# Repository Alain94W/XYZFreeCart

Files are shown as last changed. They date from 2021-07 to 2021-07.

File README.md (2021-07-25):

## XYZ Davinci FreeCart

If you are like me bored about having to reset the cartridge chip with an external computer, then this git can maybe help you.

<b> DISCLAIMER
  
I will take no responsibilities about what you are doing with this or what will happen with this, if you burn your printer, get injury or everything else, don't blame me, your choice, your responsibilities.
I made it for fun, it is working well on my printer (DaVinCi AIO 1.0), I only share for free my work and by the way I don't want to see this work being resell on ebay or on other eshop web site.
</b>

That said ...

<p align="center" width="100%">
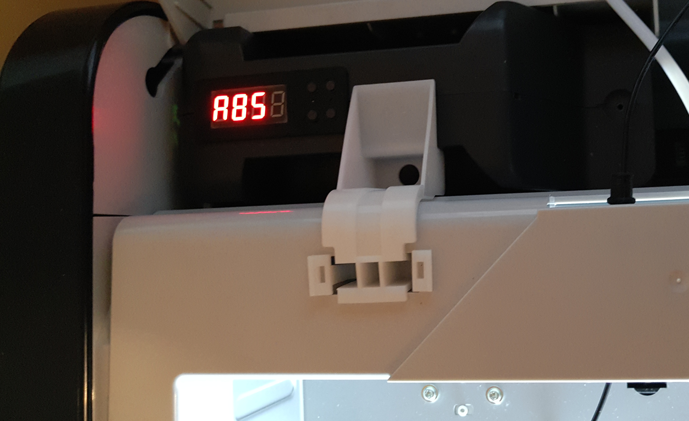
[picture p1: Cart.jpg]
cart
  
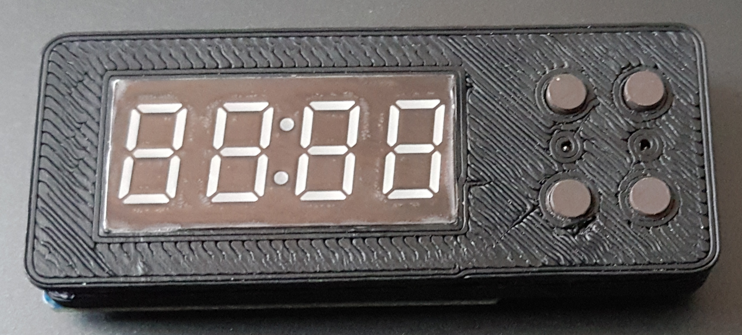
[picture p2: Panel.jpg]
  
</p>

## History of the project
I was using for a long time the arduino reseter made by votivo (by the way, thanks to him for he's work), I was stuck on a PLA filament bought on Amazon (Amazon Basics) The filament always clog the nozzle, I had to play a lot with the extruder temperature and all the time had to reprogram the cartridge chip.
To get ride of this, I used a raspberry pico and a 4*7 Digit LED display (TM1637) and using 4 buttons, I made an EEPROM emulator that I put directly inside the original cartridge.

## The Arm choice 

Because I need a fast microcontroller, cheap and 3.3V level for that task, I've choose the Raspberry Pi Pico.
The raspberry pico is very powerful, but to achieve my project, I had to overclock it to 291MHz and to use both core to run the code.
On Core 0, the UNIO Slave driver is running, waiting for some command coming from the printer (not using pio because of the UNIO protocol specifications). 
On Core 1, the button and display are handled.

The content of the original EEPROM was dump from a PLA's cartridge chip and is written in the flash memory of the pico. When the program start, the FLASH is loaded into the RAM, every time the printer is writing the length update into the cartridge chip, the pico update it's RAM then save it to it's FLASH.

The TM1637 (bought on Amazon) is used to allow the user to changes this settings directly from the cartridge:

<li> Bed Temperature </li>
<li> Extruder Temperature </li>
<li> Filement color </li>
<li> Type of Material </li>
<li> Display and or reset the remaining filament length </li>

When changing bed/extruder temp or color, you can save this settings as a profile for the selected material, there is already a set of profile made in the pico for example :

<li>ABS => Bed : 90*C, Extruder : 210*C, Color : Green </li>
<li>PLA => Bed : 45*C, Extruder : 195*C, Color : Yellow </li>

The available material are :

<li>ABS</li>
<li>PLA</li>
<li>FLEX</li>
<li>PETG</li>
<li>Water Soluble</li>
<li>UVCR</li>
<li>NYLON</li>
<li>ASA</li>

The are 4 buttons used to select the menu, change settings and reset the length:

* SEL : Choose menu (Bed, Head, Colo, Mat, Fil)
* UP/DOWN : to increase and decease the values or change items
* RESET : press less than 3sec => Save settings in the FLASH, Press >3s, reset the spool len and change the serial number.

If you have an unknown filament error on the printer, just press 4sec the Reset button, this will change the serial number.
Every changes made in the menu should be immediately visible in the cart INFO menu of the printer.
Do not reset or change the settings while the printer is printing as it may fail your printing job.

## Printer firmware

I'm using the original factory shipped firmware on my printer, it is an old one, the version <b>1.1.3</b>, I didn't test this on other version or printer model.

## Installation

First, this suppose that you already follow the raspberry pi procedure and you already have the pico-sdk installed.
Then, git clone this repo and go into the root folder.

Edit the CMakeLists.txt on line 10, change the SDK path with your own SDK Path.

Run the following command to compil the pico code :

```
mkdir build
cd build
cmake ..
make
```

This will end up and create a freecart.uf2 file that you can load via the USB to the pico (in boot mode).

<b> NEVER CONNECT THE USB HOST ON THE PICO WHILE IT IS CONNECTED TO THE PRINTER, the printer is 3.3V level and the main board will be destroyed by the 5V injection coming from the USB over the VSYS line of the PICO. </b> If you really want to connect both, read carefully the pico's datasheet, thee are some solution using external schotky diode or mosfet.

## TM1637 Display driver

I used a library made by wahlencraft to drive the TM1637 display, you can find more information here on it's github : https://github.com/wahlencraft/TM1637-pico.git

Thanks for this work, it is included in this repo but I would like to credit wahlencraft for that work.

## Assembly

The step files are in this repo.
I printed them in ABS with a fill density of 50% and a layer height of 0.3 with support material.
You need to cut the cartridge where you want place the control panel, over the EEPROM PCB to make a path for the cables.

<p align="center" width="100%">
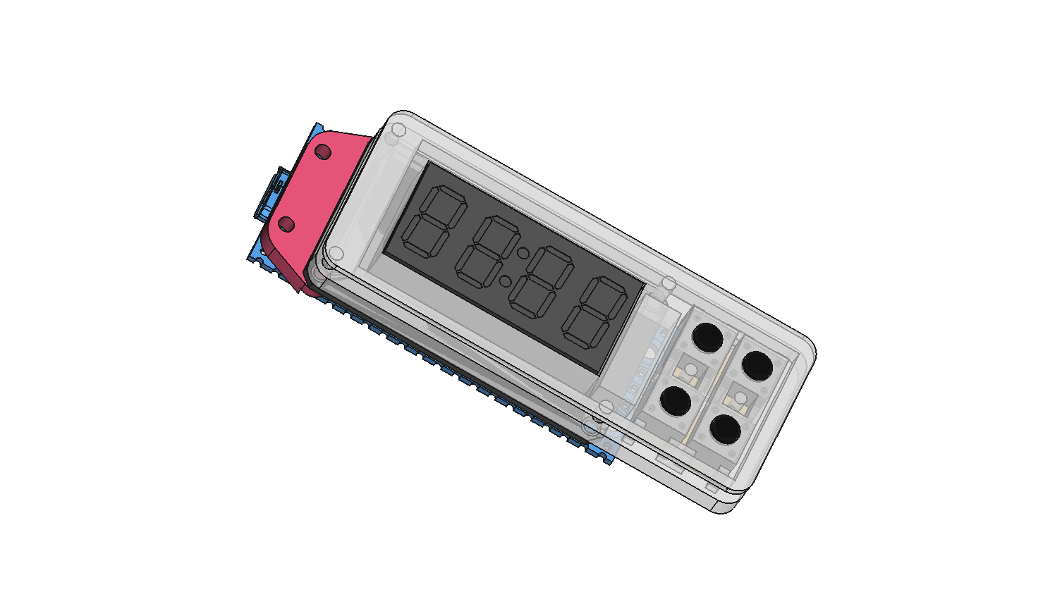
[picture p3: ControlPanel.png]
3dparts
  
</p>

<p align="center" width="100%">
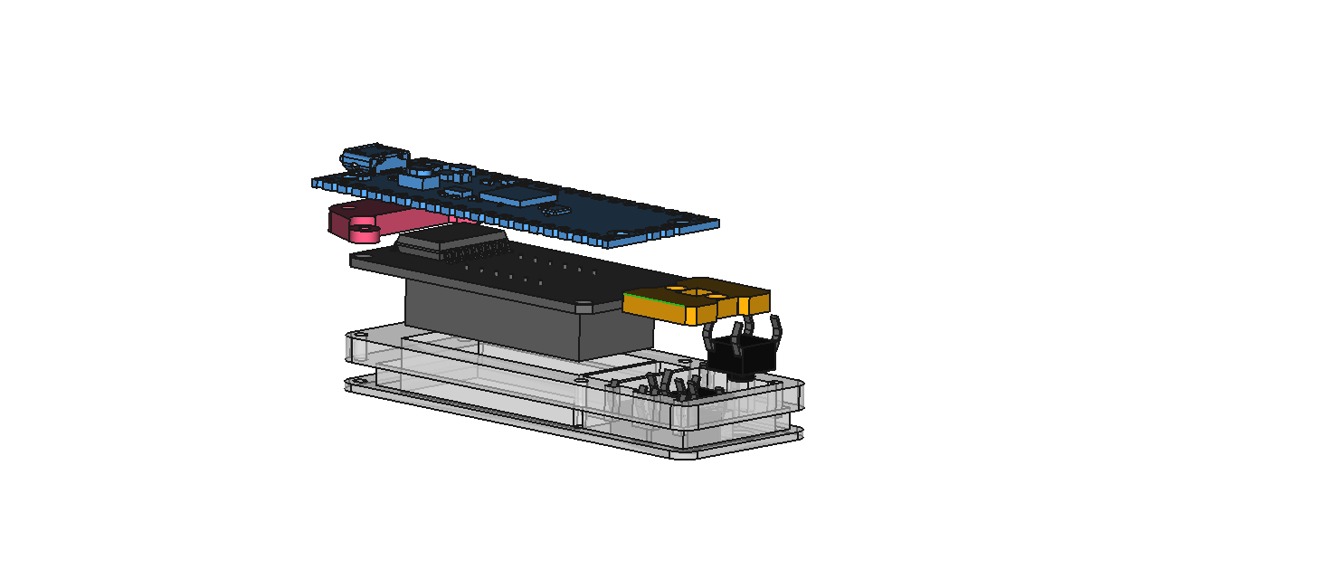
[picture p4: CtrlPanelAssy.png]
Assy
  
</p>

<p align="center" width="100%">
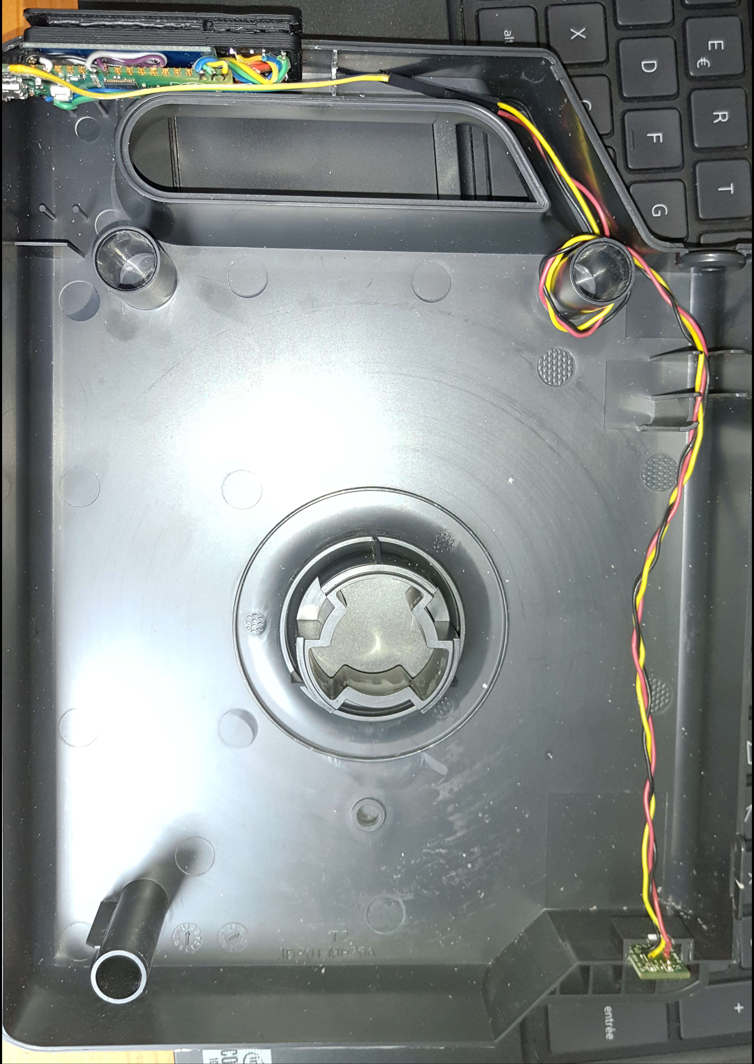
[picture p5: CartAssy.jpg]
Assy
  
</p>

You will need to "sacrifice" an original EEPROM from one of your cartridge, you will have to remove the EEPROM from the PCB and to solder 3 wire directly in place of.

<p align="center" width="100%">
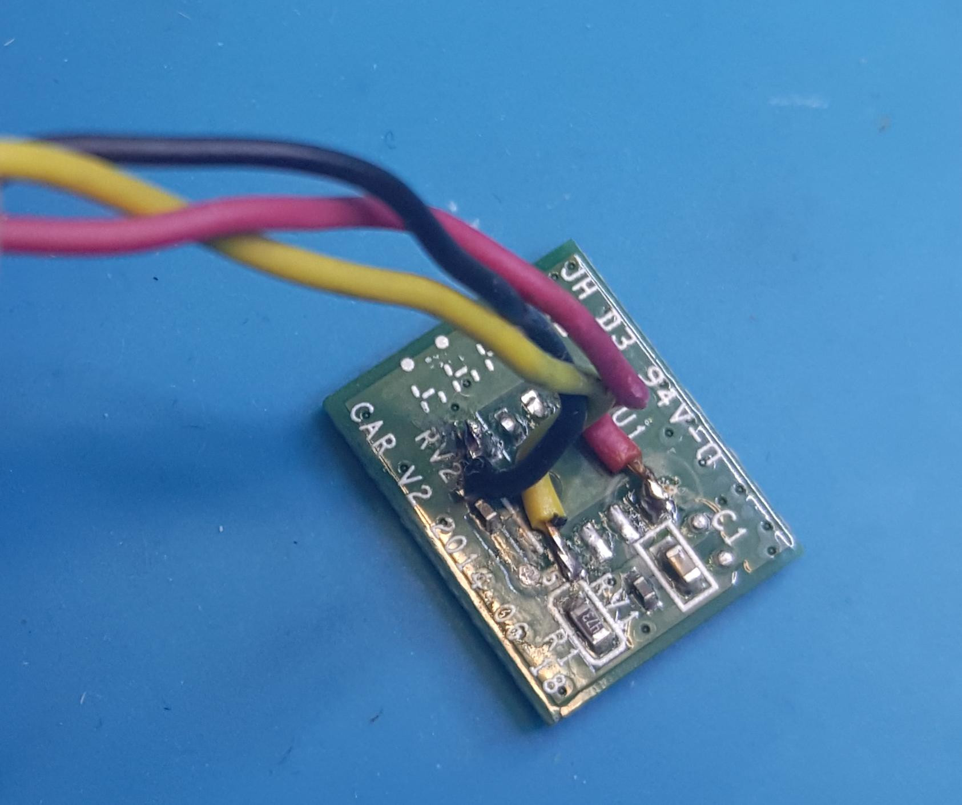
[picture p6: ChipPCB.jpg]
  
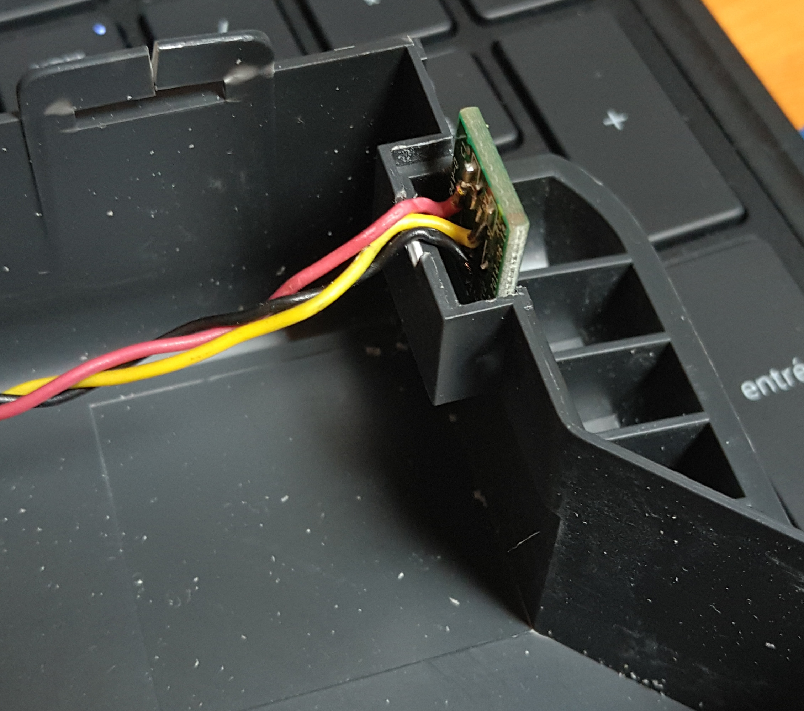
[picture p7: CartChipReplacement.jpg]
  
</p>

You have to wire everything like this:

<p align="center" width="100%">
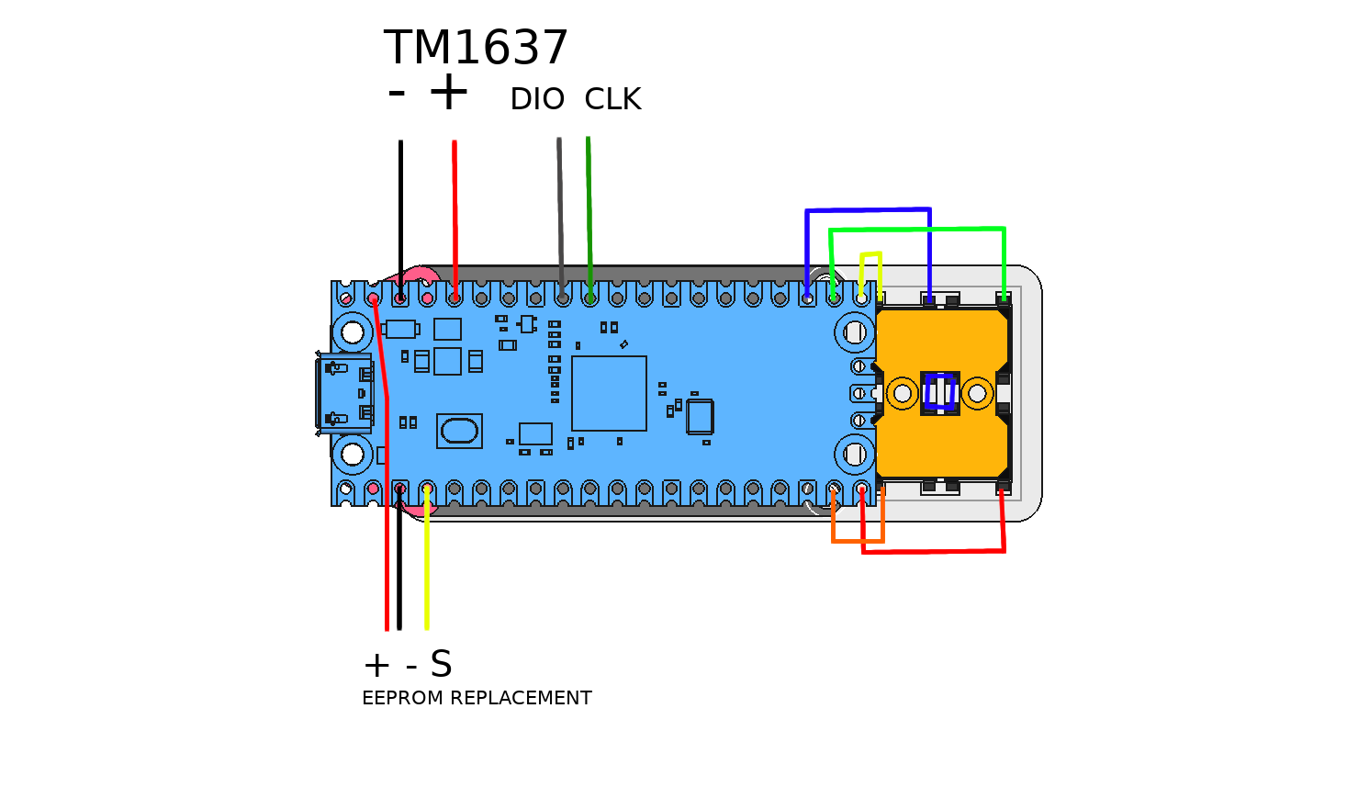
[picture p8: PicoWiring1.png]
picowiring
  
</p>

## Button disposition

<p align="center" width="100%">
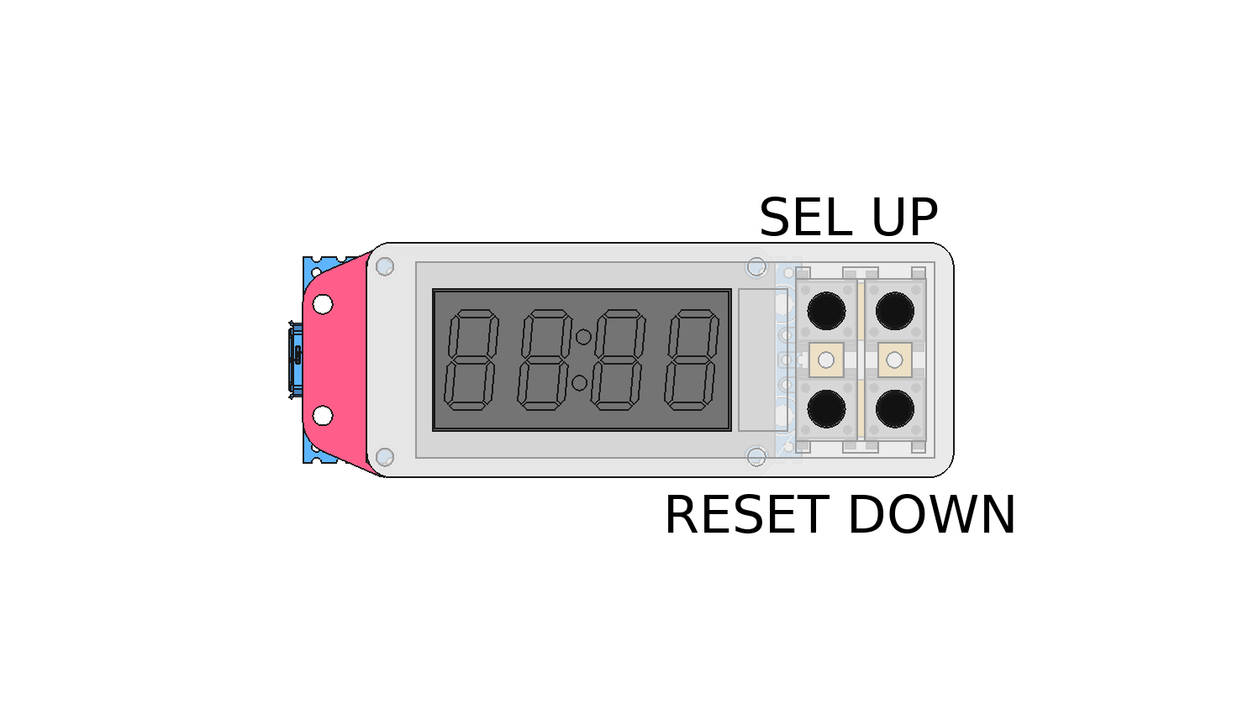
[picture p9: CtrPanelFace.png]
  
</p>

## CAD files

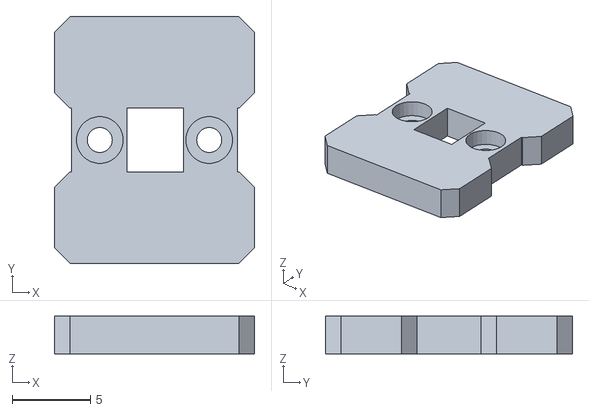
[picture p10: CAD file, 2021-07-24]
3DParts/ControlPanel-BtnLockPlate.stl
12.8 x 15.8 x 2.40

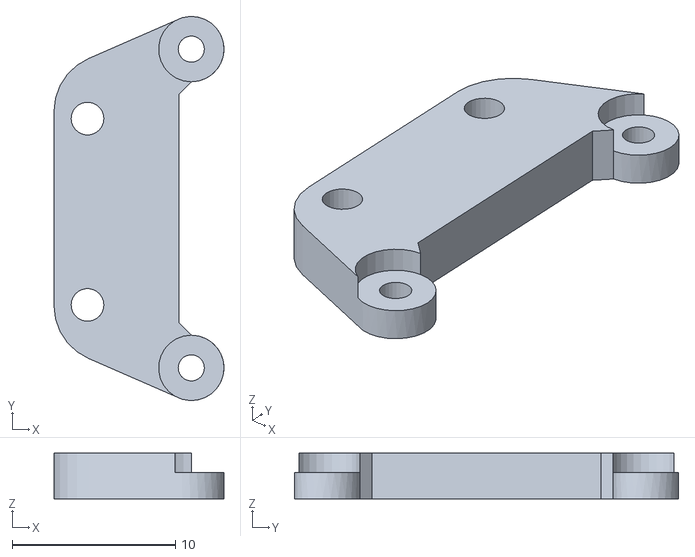
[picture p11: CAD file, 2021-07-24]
3DParts/ControlPanel-PicoFixPlateUSBSide.stl
10.4 x 23.5 x 2.80

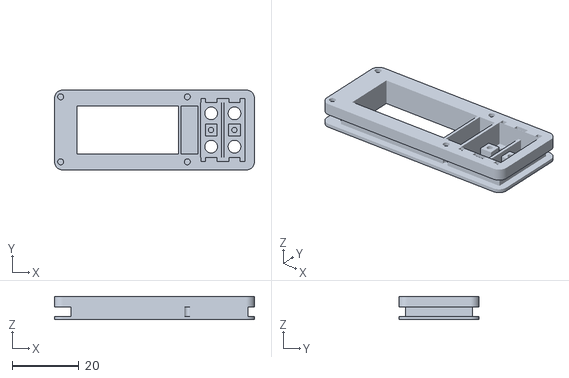
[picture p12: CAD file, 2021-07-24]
3DParts/ControlPanel-BodyPocket006.stl
60.0 x 24.0 x 7.00

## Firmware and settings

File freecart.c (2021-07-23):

#include <stdio.h>
#include <string.h> // memcpy
#include <stdlib.h> //atol
#include "pico/stdlib.h"
#include "hardware/pio.h"
#include "hardware/timer.h"
#include "hardware/clocks.h"
#include "hardware/gpio.h"
#include "pico/multicore.h"
#include <PicoTM1637.h>
#include "hardware/vreg.h"
#include "hardware/flash.h"


// End of PROGRAM IN FLASH
//  objdump --all testawe.elf | grep flash_binary_end
//   1000b78c g       .ARM.attributes	00000000 __flash_binary_end


// UNIO Doc : https://ww1.microchip.com/downloads/en/DeviceDoc/22067J.pdf

// Via openocd : openocd -f interface/raspberrypi-swd.cfg -f target/rp2040.cfg -c "program blink/blink.elfverify reset exit"


// TM 7 SEG :
//  _ a
//f|_|b G
//e|_|c
//  d

// Bit : 0000 0000
// Seg : .GFE DCBA

// Ex A = 0x77 = 0111 0111
//    B = 0x7F
//    b = 0x7C
//    e = 0x7B
//    d = 0x5E
//    H = 0x76
//    a = 0x5f 767b5f5e
//    C = 0x39
//    o = 0x5C
//    l = 0x18  0x395c185c
//    M = 0x37
//    t = 0x78  0x00375f78
//    F = 0x71
//    i = 0x10 00181071
//    S = 0x6D 006D7F77
//    P = 0x73
//    L = 0x38 00773873
//    E = 0x79  00793871
//    G = 0x7D PETG = 7D787973
//    U = 0x3E SOLU = 3E387E6D
//    O = 0x3F //7E
//    n = 0x54
//    Y = 0x72
//    r = 0x50
//    v = 0x1C
//    - = 0x40

// UVCR = 50391C3E

//    rdy = 00725E72
//    nYLO = 7E38721C
//    GrEy = 7279507D
//    GrEE = 7979507D 
//    BLAC = 3977387C
//    WHIt = 7810763E
//    YELL = 38387972
//    bLUE = 793E387C
//    rEd  = 005E7950
//    nAt  = 0078771C
//    CLEA = 77793839
//    PUrP = 73503E73


#define LED             25
// TM
#define CLK_PIN         26
#define DIO_PIN         27

// UNIO
#define UNIO_PIN        2
#define PULSE_PIN       3
#define DBG_PIN         4
#define MIN_STDB_PUSLE  590 // Standby pulse time

#define UNIO_HEADER     0x55
#define CMD_RDSR        0x05
#define CMD_WRSR        0x6E
#define CMD_READ        0x03
#define CMD_CRRD        0x06
#define CMD_WRITE       0x6C
#define CMD_WREN        0x96
#define CMD_WRDI        0x91
#define CMD_ERAL        0x6D
#define CMD_SETAL       0x67

#define EST_T           18
#define DEVICE_ADDR     0xA0

// For UNIO Timing
int64_t T=0;

// BTN
#define BTN_SEL         14
#define BTN_UP          15
#define BTN_DOWN        17
#define BTN_RAZ         16

#define FALL            0x04
#define RISE            0x08


uint8_t MENU  =         0;

/* UNIO EEPROM REGISTERS */
uint8_t STATUS_REGISTER = 0;
uint16_t ADDR_START = 0;
uint8_t EEPROM[1024]= {0x5A,0x41,0x4B,0x00,0x00,0x35,0x32,0x54,0x80,0xA9,0x03,0x00,0x80,0xA9,0x03,0x00,
                       0xFA,0x00,0x5A,0x00,0x54,0x48,0x47,0x42,0x30,0x33,0x35,0x37,0x00,0x00,0x00,0x00,
                       0x00,0x00,0x00,0x00,0x34,0x00,0x00,0x00,0x00,0x00,0x00,0x00,0xAA,0x55,0xAA,0x55,
                       0x88,0x33,0x55,0xAA,0x51,0x44,0x02,0x00,0x00,0x00,0x00,0x10,0x04,0xED,0x00,0xE0,
                       0x5A,0x41,0x4B,0x00,0x00,0x35,0x32,0x54,0x80,0xA9,0x03,0x00,0x80,0xA9,0x03,0x00,
                       0xFA,0x00,0x5A,0x00,0x54,0x48,0x47,0x42,0x30,0x33,0x35,0x37,0x00,0x00,0x00,0x00,
                       0x00,0x00,0x00,0x00,0x34,0x00,0x00,0x00,0x00,0x00,0x00,0x00,0xAA,0x55,0xAA,0x55,
                       0x88,0x33,0x55,0xAA,0x80,0xA9,0x03,0x00,0xAA,0x55,0xAA,0x55,0x1F,0x0E,0x0B,0x00, // End of Cartdrige Data
                       0x01,0x00,0x00,0x00,0x00,0x00,0x00,0x00,0x00,0x00,0x00,0x00,0x00,0x00,0x00,0x00, // Blank line
                       90  ,210 ,0x00,0x47,100 ,250 ,0x00,0x4B,70  ,230 ,0x00,0x57, 45 ,195 ,0x00,'Y' , // First profile line
                       45  ,195 ,0x00,0x42, 100,250 ,0x00,0x52, 45 ,205 ,0x00,0x5A, 50 ,210 ,0x00,0x41,
                       45  ,180 ,0x00,0x33, 80 ,240 ,0x00,0x31,0x00,0x00,0x00,0x00,0x00,0x00,0x00,0x00
                      };

#define   PROFILE_START 0x90
#define   OFFSET_BED    0x00
#define   OFFSET_EXT    0x01
#define   OFFSET_COLO   0x03
#define   PROFILE_SIZE  4

#define   SN            0x18
#define   BEDTEMP       0x12
#define   EXTTEMP       0x10
#define   MATERIAL      0x01
#define   COLOR         0x02
#define   TOTLEN        0x08
#define   NEWLEN        0x0C
#define   LEN2          0x34
#define   OFFSETMEM     0x40

#define   MAX_EXTTEMP   260
#define   MIN_EXTTEMP   50
#define   MAX_BEDTEMP   110
#define   MIN_BEDTEMP   0

#define FLASH_STORAGE   0xf000
#define FLASH_SIZE      1024

volatile int blink=0;
static int64_t interval;
uint8_t nbwr = 0;
uint8_t LOCKED = 0;



const uint8_t MaterialList[] = {
  'A',    // 0
  'F',    // 1
  'G',    // 2
  'P',    // 3
  'Q',    // 4
  'S',    // 5
  'T',    // 6
  'U',    // 7
  'V',    // 8
  'Y'    // 9
  };


const uint8_t ColorList[] = {
  0x31,    // 0
  0x47,    // 1
  0x4B,    // 2
  0x57,    // 3
  0x59,    // 4
  0x42,    // 5
  0x52,    // 6
  0x5A,    // 7
  0x33,    // 8
  0x41     // 9
  };

static const char *gpio_irq_str[] = {
        "LEVEL_LOW",  // 0x1
        "LEVEL_HIGH", // 0x2
        "EDGE_FALL",  // 0x4
        "EDGE_RISE"   // 0x8
};

static char event_str[128];


void doSAK3 ();
uint8_t getBit();
uint8_t getByte (uint8_t *MAKout);

void SaveVirtualEEPROM();
void ReadEEPROM ();
void initBtn();

void gpio_event_string(char *buf, uint32_t events);
void unioevent_callback(uint gpio, uint32_t events);



// Disable int
void DisableInt()
{
  gpio_set_irq_enabled(UNIO_PIN,GPIO_IRQ_EDGE_RISE | GPIO_IRQ_EDGE_FALL,false);
  gpio_acknowledge_irq(UNIO_PIN,GPIO_IRQ_EDGE_RISE | GPIO_IRQ_EDGE_FALL);
}



void putBit (bool bit)
{
  gpio_put(UNIO_PIN, !bit);
  // Attend 1T
  busy_wait_us(T+2);
  gpio_put(UNIO_PIN, bit);
  // Attend 1T  
  busy_wait_us(T+2);
}


uint8_t getByte (uint8_t *MAKout)
{
  uint8_t tes = 0;
  for (int y =0;y<8;y++)
  {
      uint8_t bi = getBit();
      tes = (tes << 1) + bi; 
  }

  *MAKout = getBit();
  doSAK3();
  return tes;
}


// Traitement de la commande reçue
void TreatCMD2 (uint8_t cmd)
{
  uint8_t Data = 0x55;
  //UnioLastCmd = cmd;
  DisableInt();

  switch (cmd)
  {
  case CMD_RDSR :
  {
    
    Data = STATUS_REGISTER;

    gpio_set_dir(UNIO_PIN, GPIO_OUT);
    for (int i=0;i<8;i++)
      putBit((Data<<i) & 0x80);
    gpio_set_dir(UNIO_PIN, GPIO_IN);

    uint8_t MAK = getBit();
    doSAK3();

    //UnioStatus = IDLE;
    break;
  }

  case CMD_WRSR :
  {
    uint8_t MAKed = 0;

    STATUS_REGISTER = getByte (&MAKed);

    //UnioStatus = IDLE;
    break;
  }

  case CMD_READ :
  {
    //UnioStatus = ARG1;
    //AddrComplet = false;

    uint8_t MAKed = 0;
    ADDR_START = getByte (&MAKed);

    if (MAKed==1)//MAK
      {
        ADDR_START = (ADDR_START<<8) + getByte (&MAKed);
        if (MAKed == 1)
          {
            // Envois jusqu'au NoMAK

            ReadEEPROM();
            
            while (getBit() == true)
              {
                doSAK3();
                ADDR_START++;
                ReadEEPROM();
              }

            doSAK3();
          }
      }

    //UnioStatus = IDLE;
    break;
  }

  case CMD_WRITE:
  {
    uint8_t MAKed = 0;

    ADDR_START = getByte (&MAKed);
    uint16_t adstrbackup = ADDR_START;

    if (MAKed==1)//MAK
      {
        ADDR_START = (ADDR_START<<8) + getByte (&MAKed);
        adstrbackup = ADDR_START;
        nbwr=0;
        while (MAKed == 1) 
        {
          if ((ADDR_START>=0) && (ADDR_START<1024))
            {
              EEPROM[ADDR_START] = getByte (&MAKed);
              ADDR_START++;
              nbwr++;
            }
        }

        interval = time_us_64();
        while ((time_us_64()-interval)<=(T)) {};
        ADDR_START = 0;
        LOCKED=0; // Free up the lock
        //printf("%X",adstrbackup);
        if (adstrbackup == 0x70)
        {
          SaveVirtualEEPROM(); // Write only if we are updating the last part of the EEPROM,
                               // Otherwise the print will fail because this procedure take too much time.
                               // We also reduce the write action to the FLASH to preserve it's life a little.
          printf("W\r\n");
        }
      }
    break;
  }

  case CMD_WREN :
      // We don't care about this.
    break;

  default:
    // Ohoh
    printf("UNKNOWN COMMAND : %X\r\n",cmd);
    break;
  }

return;
}


// Slave ACK
void doSAK3 ()
{
  // Low the Pin for 1T
  gpio_put(DBG_PIN,true);
  gpio_put(PULSE_PIN,true);
  gpio_set_dir(UNIO_PIN,GPIO_OUT);
  gpio_put(UNIO_PIN,false);
  
  // Attend 1T
  interval = time_us_64();
  while ((time_us_64()-interval)<=T) {}

  // Acquitte
  
  gpio_put(UNIO_PIN,true);
  
  // Attends 1T
  interval = time_us_64();
  while ((time_us_64()-interval)<=T) {} // ok +Jit
  
  gpio_put(UNIO_PIN,false);
  gpio_set_dir(UNIO_PIN,GPIO_IN);

  gpio_put(PULSE_PIN,false);

  gpio_acknowledge_irq(UNIO_PIN,GPIO_IRQ_EDGE_RISE | GPIO_IRQ_EDGE_FALL);

  gpio_put(DBG_PIN,false);
}


// AW 27052021 
// Routine De lecture d'un bit en restant synchro sur le changement de front
// OK
uint8_t getBit ()
{
//gpio_put(PULSE_PIN,true);
  bool a,b=0;
  uint64_t T2 = T/2;
  // Attend 1/2 T
  interval = time_us_64();
  busy_wait_us(T2);
  // Lit la valeur du bit
  a = gpio_get(UNIO_PIN);
  // Attend 1T
  while ((gpio_get(UNIO_PIN) == a)){};// && (time_us_64()-interval<=(T))) {}
  // Récup la valeur
  b = gpio_get(UNIO_PIN);
  // On est synchro sur MAK, attend 1/2 T
  busy_wait_us(T);
  return bool_to_bit(b && !a);
}


void ReadEEPROM ()
{
  //gpio_put(PULSE_PIN,true);
  gpio_set_dir(UNIO_PIN, GPIO_OUT);
  for (int i=0;i<8;i++)
    putBit((EEPROM[ADDR_START]<<i) & 0x80);
  gpio_set_dir(UNIO_PIN, GPIO_IN);
  //gpio_put(PULSE_PIN,false);
  //interval = time_us_64();
  busy_wait_us(2);
}




//alarm_id_t id, void *user_data) {
bool alarm_callback(struct repeating_timer *t) {
  //printf("Repeat at %lld\n", time_us_64());
  // Put your timeout handler code in here
  gpio_put(LED,blink);
  blink = ~blink;
  return true;
}



void usdelay (uint64_t us)
{
  interval = time_us_64();
  while ((time_us_64()-interval)<=us) {};
}



void initTMS()
{
  TM1637_init(CLK_PIN, DIO_PIN);  
  TM1637_clear(); 

  TM1637_set_brightness(7); // max value, default is 0
  TM1637_put_4_bytes(1, 0x00725E50);  // raw bytes for rdY 
  usdelay(1000000);
}


// Convert input Material code to Digit for TM display
void MatToDigit(uint8_t Mat)
{
  switch (Mat)
  {
  case 'A':
    /* ABS */
    TM1637_put_4_bytes(0, 0x006D7F77);
    break;
  case 'F':
    /* FLEX */
    TM1637_put_4_bytes(0, 0x00793871);
    break;    
  case 'G':
    /* PETG */
    TM1637_put_4_bytes(0, 0x7D787973);
    break;   
  case 'P':
    /* PLA 1*/
    TM1637_put_4_bytes(0, 0x00773873);
    break;
  case 'Q':
    /* PLA 2 Metal FREE*/
    TM1637_put_4_bytes(0, 0x71773873);
    break;    
  case 'S':
    /* ASA */
    TM1637_put_4_bytes(0, 0x00776D77);
    break;   
  case 'T':
    /* Tough PLA */
    TM1637_put_4_bytes(0, 0x76773873);
    break;
  case 'U':
    /* UVCR */
    TM1637_put_4_bytes(0, 0x50391C3E);
    break;
  case 'V':
    /* WATER SOLUBLE */
    TM1637_put_4_bytes(0, 0x3E383F6D);
    break;
  case 'Y':
    /* NYLON */
    TM1637_put_4_bytes(0, 0x3F387254);
    break;
  default:
    TM1637_put_4_bytes(0, 0x40404040);
    break;
  }
}


// Convert Color code to Digit for TM Display
void ColoToDigit(uint8_t Colo)
{
  switch (Colo)
  {
  case 0x31:
    /* Grey */
    TM1637_put_4_bytes(0, 0x7279507D);
    break;
  case 0x47:
    /* GREEN */
    TM1637_put_4_bytes(0, 0x7979507D);
    break;    
  case 0x4B:
    /* BLACK */
    TM1637_put_4_bytes(0, 0x3977387C);
    break;   
  case 0x57:
    /* WHITE */
    TM1637_put_4_bytes(0, 0x7810763E);
    break;
  case 0x59:
    /* YELLOW */
    TM1637_put_4_bytes(0, 0x38387972);
    break;    
  case 0x42:
    /* BLUE */
    TM1637_put_4_bytes(0, 0x793E387C);
    break;   
  case 0x52:
    /* RED */
    TM1637_put_4_bytes(0, 0x005E7950);
    break;
  case 0x5A:
    /* NATURE */
    TM1637_put_4_bytes(0, 0x00787754);
    break;
  case 0x33:
    /* CLEAR */
    TM1637_put_4_bytes(0, 0x77793839);
    break;
  case 0x41:
    /* PURPLE */
    TM1637_put_4_bytes(0, 0x73503E73);
    break;
  default:
    TM1637_put_4_bytes(0, 0x40404040);
    break;
  }
}

// Increment the eeprom serial number (comes from arduino code from volvito)
uint32_t IncSN()
{
  char Ser[5] = {0};
  sprintf(Ser,"%c%c%c%c", EEPROM[SN],EEPROM[SN+1],EEPROM[SN+2],EEPROM[SN+3]);
  uint32_t serial = atol(Ser);
  serial++;
  sprintf(Ser,"%04d",serial);
  memcpy(&EEPROM[SN],Ser, 4);
  printf("New SN:%s\r\n",Ser);
}


// Return the index corresponding to the current material, very usefull.
uint8_t GetCurrentMatIndex()
{
  for (int i=0;i<10;i++) 
    if (MaterialList[i] == EEPROM[MATERIAL])
      {
        return i;
      }
  return 0;
}
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
int main()
{
    //set_sys_clock_khz(270000, true);
    
    // !!! OVERCLOCK the PICO to 291MHz !!!
    vreg_set_voltage(VREG_VOLTAGE_1_15);
    sleep_ms(1000);
    set_sys_clock_khz(291000, true);
    sleep_ms(200);

    stdio_init_all();

    // Start TM control over Core 1
    multicore_launch_core1(core1main);

    // LED
    gpio_init(LED);
    gpio_set_dir(LED,GPIO_OUT);
    gpio_put(LED,1);

    
    sleep_ms(2000);
    puts("System Ready.\r\n");
    LoadVirtualEEPROM ();
    initUnio();
    
  
    // Core 0 will handle UNIO Driver
    bool bit = gpio_get(UNIO_PIN);

    // Tbit = 18us on the Davinci with the pico as slave receiver.
    T = EST_T;

    while(1)
    {
      interval = time_us_64();
      // Look for the long high level (stdby pulse)
      LOCKED = 0;
      while (gpio_get(UNIO_PIN) == 1) {}
      //printf("t:%lld\r\n",time_us_64() - interval);
      if (((time_us_64() - interval) >=90) && ((time_us_64() - interval) <6500))
        {
          LOCKED = 1;
          interval = time_us_64();
          while (gpio_get(UNIO_PIN) == 0) {} // Repasse à 1
          
          //printf("t:%lld\r\n",time_us_64() - interval); 
          gpio_put(PULSE_PIN,true);

          // READ HEADER
          uint8_t tes = 0;
          for (int y =0;y<8;y++)
          {
              uint8_t bi = getBit();
              tes = (tes << 1) + bi; 
          }
          
          uint8_t MAK = getBit(); // ok
          //printf("Header : %X,%lld\r\n",tes,T);
          gpio_put(PULSE_PIN,false);

          if (tes != UNIO_HEADER) 
            {
              printf("f,%X,%lld\r\n",tes,time_us_64()-interval);
              continue;
            }
          else
            {
              // NoSAK, bien placée, OK
              busy_wait_us(T*2);
              
              gpio_put(PULSE_PIN,true);

              // READING ADDRESS
              uint8_t tes = 0;
              for (int y =0;y<8;y++)
                {
                    uint8_t bi = getBit();
                    tes = (tes << 1) + bi; 
                }
              
              gpio_put(PULSE_PIN,false);
              
              if (getBit()==1)//MAK
                {
                  if (tes != DEVICE_ADDR) 
                    {
                      printf("WRONG DEVICE ADDR %X\r\n", tes);
                      while (bit == 0) {bit = gpio_get(UNIO_PIN);} // AJOUT
                      continue;
                    }

                  // ACKNOWLEDGE
                  doSAK3();

                  //READING COMMAND
                  tes = 0;
                  for (int y =0;y<8;y++)
                    {
                        uint8_t bi = getBit();
                        tes = (tes << 1) + bi; 
                    }
                  if (getBit()==1)//MAK
                    {
                      // ACKNOWLEDGE
                      doSAK3();

                      // TREAT COMMAND
                      TreatCMD2(tes);

                      // WAIT UNTIL WE RECEIVE 1 AGAIN
                      while (bit == 0) {bit = gpio_get(UNIO_PIN);}
                      continue;
                    }
                  else
                    {
                      // ACKNOWLEDGE
                      doSAK3();
                      continue;
                    }
                }
              else
                {
                  // ACKNOWLEDGE
                  doSAK3();
                }
              
            }
        }

      // WAIT UNTIL WE RECEIVE 1 AGAIN
      while (bit == 0) {bit = gpio_get(UNIO_PIN);}
    };

    return 0; // You never go there
}

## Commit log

2021-07-23 Added content for TM1637 display from wahlencraft/TM1637-pico
    Source coming from https://github.com/wahlencraft/TM1637-pico
2021-07-24 Added 3DParts
    [ControlPanel-BodyPocket006.stl, ControlPanel-BtnLockPlate.stl, ControlPanel-PicoFixPlateUSBSide.stl]
